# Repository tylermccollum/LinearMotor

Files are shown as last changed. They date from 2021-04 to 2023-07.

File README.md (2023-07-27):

# Axial Linear Motor
A 3D printed linear motor prototype
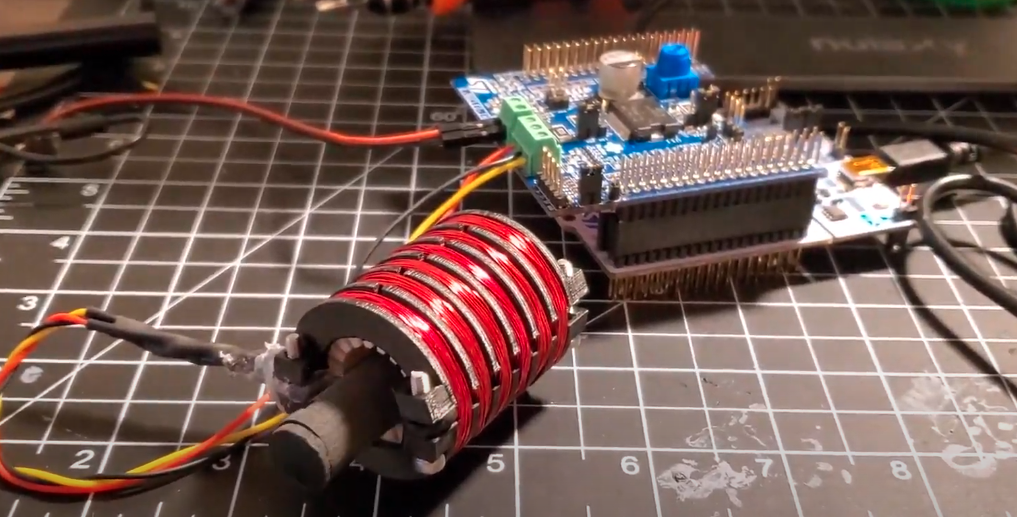
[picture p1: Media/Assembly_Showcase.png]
Assembly


# Background
While the end-goal of many actuators is linear motion, achieving linear motion usually involves a rotary motor and a ball-screw or a spool and cable assembly. While both of those options will suffice for most applications, they significantly increase the complexity of most assemblies and are susceptible to wear. "True" linear motors do exist, but most designs have the coil-magnet flux normal to the path of travel, essentially forming a rotary BLDC motor with an infinite radius. This configuration reduces the efficiency and the force output for a motor of a given size. 

While it is even possible to purchase linear motors where the flux angle is always perfectly aligned (what I'll call "Axial Flux Linear Motors") they're often prohibitively expensive outside of commercial applications and lack potential for customization. The goal for this project is to design a functional, scalable prototype of an axial linear motor that can be re-used in future designs.

# Design
The current iteration of this design is as follows:
- A metal (brass) tube (16mm OD) that will serve as the rail (or piston) for the actuator
- A 3D printed tube to fit inside the rail that will conwtain the magnets
- A polymer linear bearing (Igus 16mm ID) for ease of movement between the carriage and rail
- A carriage formed of two shells that clamp around the bearing
- Three phases of magnet wire that wind around the carriage assembly

Renderings and images of the parts can be seen below:

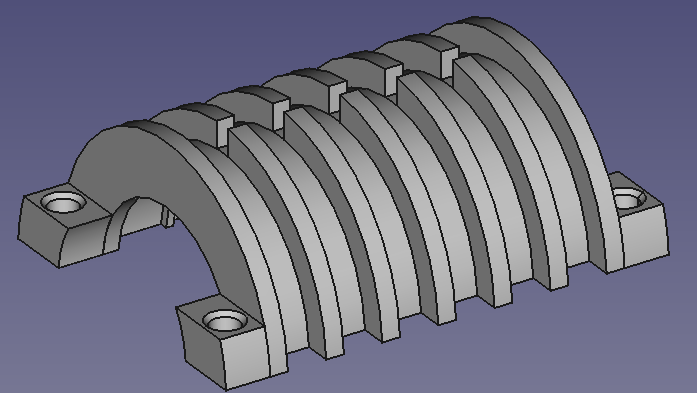
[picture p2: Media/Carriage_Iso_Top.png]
Carriage half rendering


Carriage half body

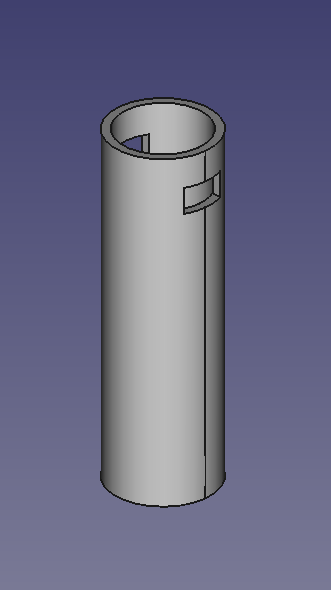
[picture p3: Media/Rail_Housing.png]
Magnet housing rendering


Magnet housing tube body

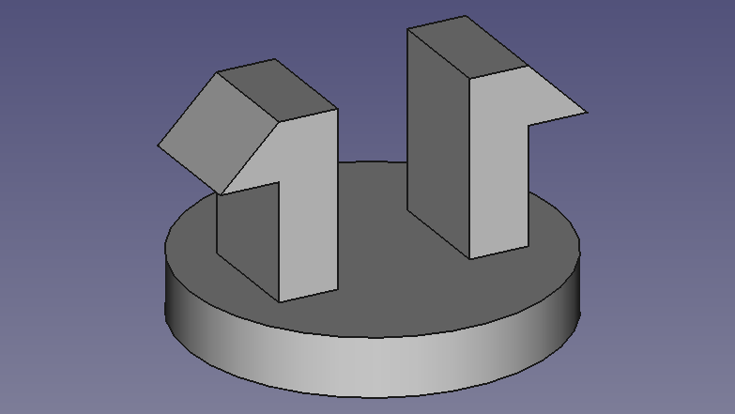
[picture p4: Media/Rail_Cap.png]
Magnet cap rendering


Magnet housing cap

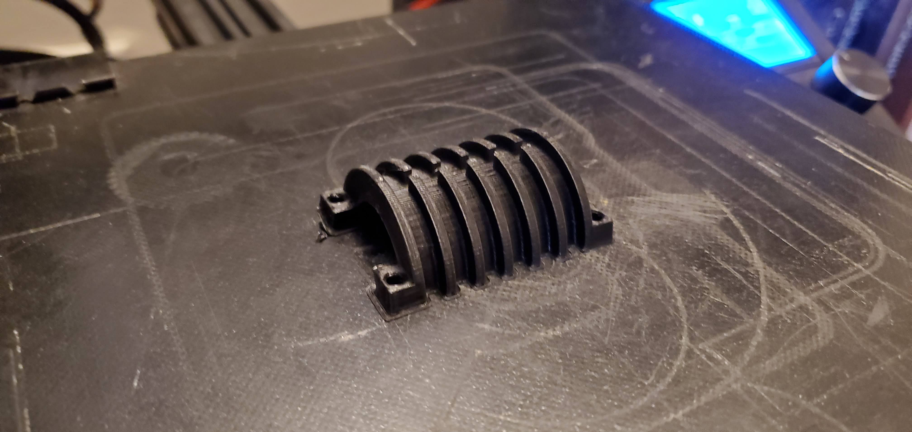
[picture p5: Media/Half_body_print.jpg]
Carriage half

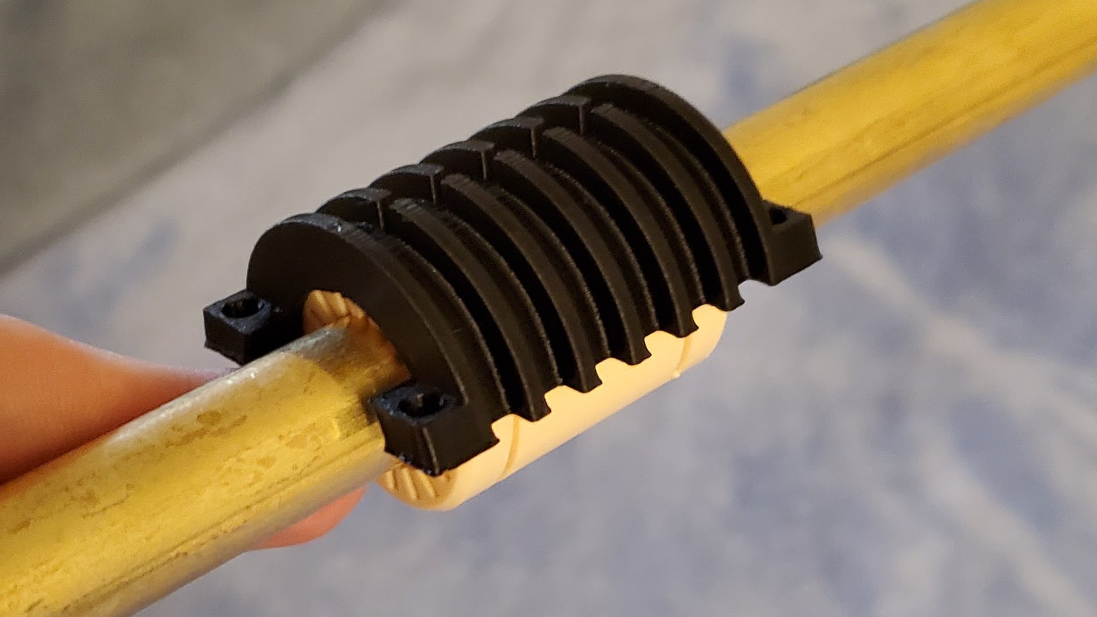
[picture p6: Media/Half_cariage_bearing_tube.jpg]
Carriage half on bearing on rail

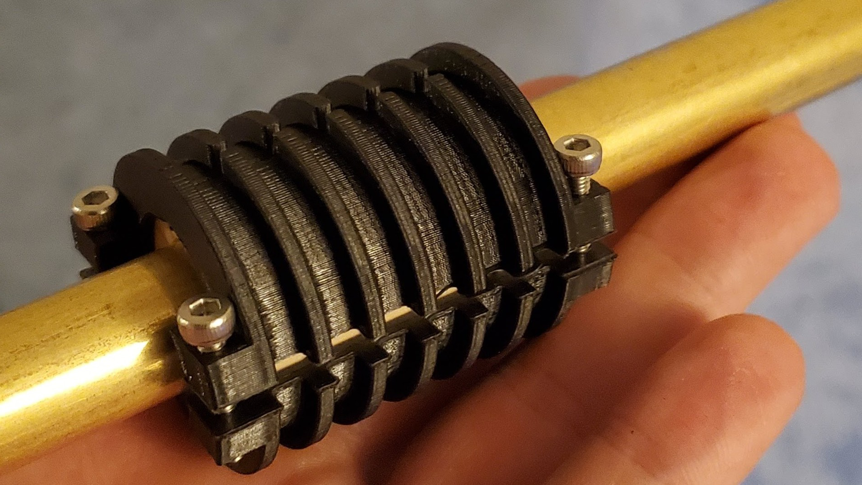
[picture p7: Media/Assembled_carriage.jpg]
Carriage assembly

Carriage with coils
Carriage with coils on rail

# Assembly
The assembly of the 3D printed carriage body is relatively straight-forward: snap the two halves around the bearing and insert 4x M3 screws to hold it together. 

## Carriage
The more difficult portion lies in the winding of the coils. While this would definitely benefit from a video, my best at describing the process is here:

1. For the first phase (A), feed the wire between the halves of the outer body and wrap one end of magnet wire around one of the clamping screws 
2. Wind the coil for as many turns as intended, choosing either clockwise or counter-clockwise *NOTE: All coils must be wound in the same direction*
3. Run the wire through the cut at the top or bottom, skipping 2 rows before bending into the channel- make sure it's in a stable position
4. Feed end of the second phase (B) between the two halves of the outer body and under the first phase, wrap around the same screw to secure
5. Begin winding the coil, ensuring that the wire from the first phase is clamped firmly under this new coil
6. When done winding, repeat step 2
7. Follow step 3, feeding the wire for phase C under both existing phases
8. Wind the coil, then run to the final open channel
9. Pull on phase A to tighten it in the first coil, then wrap the second
10. When done winding, unroll an addional length of wire approximately the length of the carriage and cut the wire from the spool
11. Run this end between the halves of the outer body and under all the coils
12. When through, pull tight to secure the second coil of phase A, then wrap carefully around the clamping screw on this end. Label this wire.
13. Repeat steps 9-12 for phases B and 
14. Tin the ends of the wires and test for phase to phase shorts
15. Twist together and solder the starting ends of the 3 phases
16. Tin, solder, and heatshrink the opposite ends for the 3 phases (I recommend color coding and, as kludgy as it feels, hot glue makes a great strain relief to avoid phase to phase shorts.
 
In the version that can be seen in the video, each coil contains 75 turns of 28AWG wire.
 
## Rail
This part, while conceptually much simpler, is a massive pain. In order to get magnetic "teeth" that the coils can hold on to, the magnets must be put together in an opposition to eachother (i.e. SN-NS-SN-NS...). This can be illustrated with some magnetic viewing film:

Aligned magnets
When aligned naturally, the poles of the magnets "short-out" and essentially form one large magnet

Opposed magnets
But when they're put together in opposition, they become seperable, allowing for the coils to hold the rail/piston in place.

To make the rail, fill the Magnet Housing with as many magnets in opposition as possible, then close the cap (you'll likely want to add glue to ensure it doesn't open, but avoid forming lumps that will catch on the carriage bearing).

The small piston seen in the video only has 4 magnets in it.

# Controls
This one certainly has room for improvement. I'm currently driving it with an X-NUCLEO-IHM07M1 kit and a basic 6-Step commutation. The current iteration of the design does not generate sufficient back-emf on movement, so some sort of encoder will be necessary (or a change to the coil setup, which is more likely)

# Conclusion
The current iteration with coils made from 75 turns of 28AWG wire and a 4 magnet piston can oscillate at up to ~3Hz when run at ~18V, ~1.2A. Exciting for a second iteration (first iteration was 9 turns of 2 24AWG strands: needed way too much current), but definitely a lot of room for improvement.

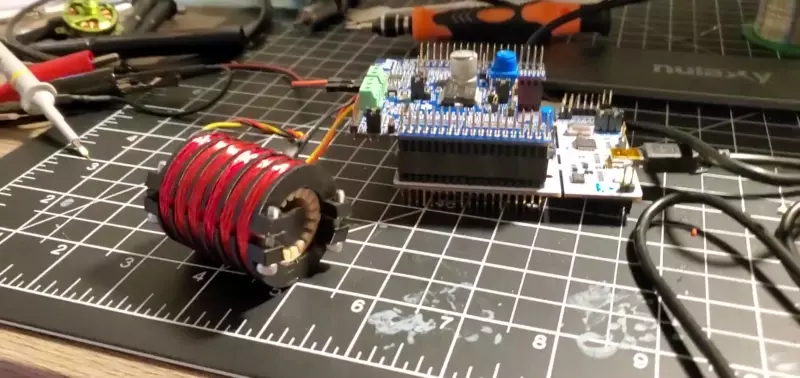
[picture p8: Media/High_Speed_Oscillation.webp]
Motor Oscillating


# Room for improvement
Theres a lot here that will need exploration:
- A greater quantity of shorter phases
- Parametric carriage generation
- More turns of thinner wire
- Stabilized magnets within the rail

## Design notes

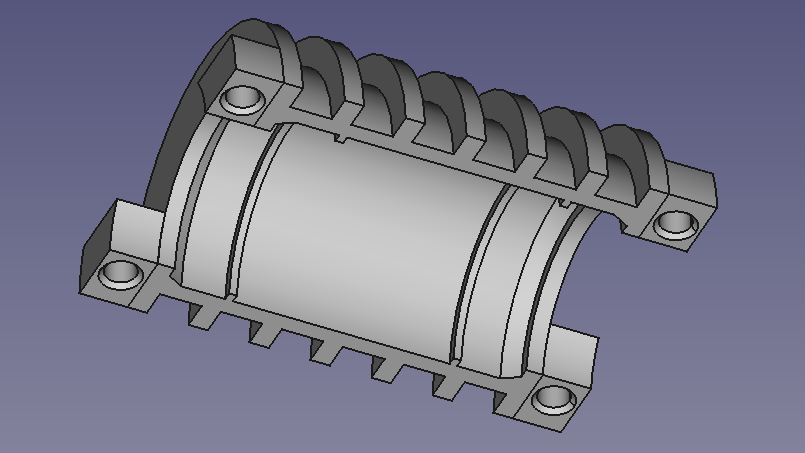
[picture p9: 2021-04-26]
Media/Carriage_Iso_Bottom.png

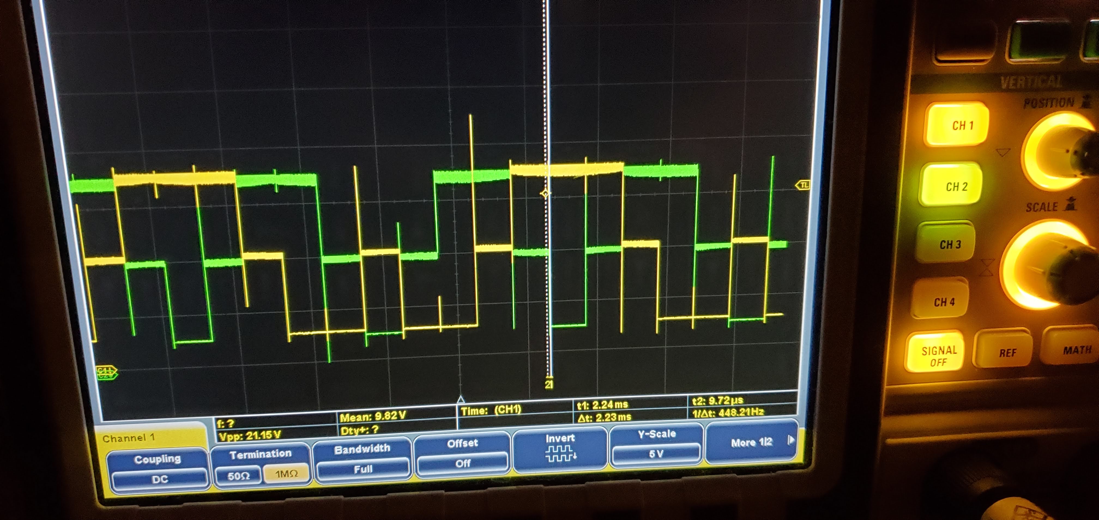
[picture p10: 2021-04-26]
Media/Phase_Voltages.jpg

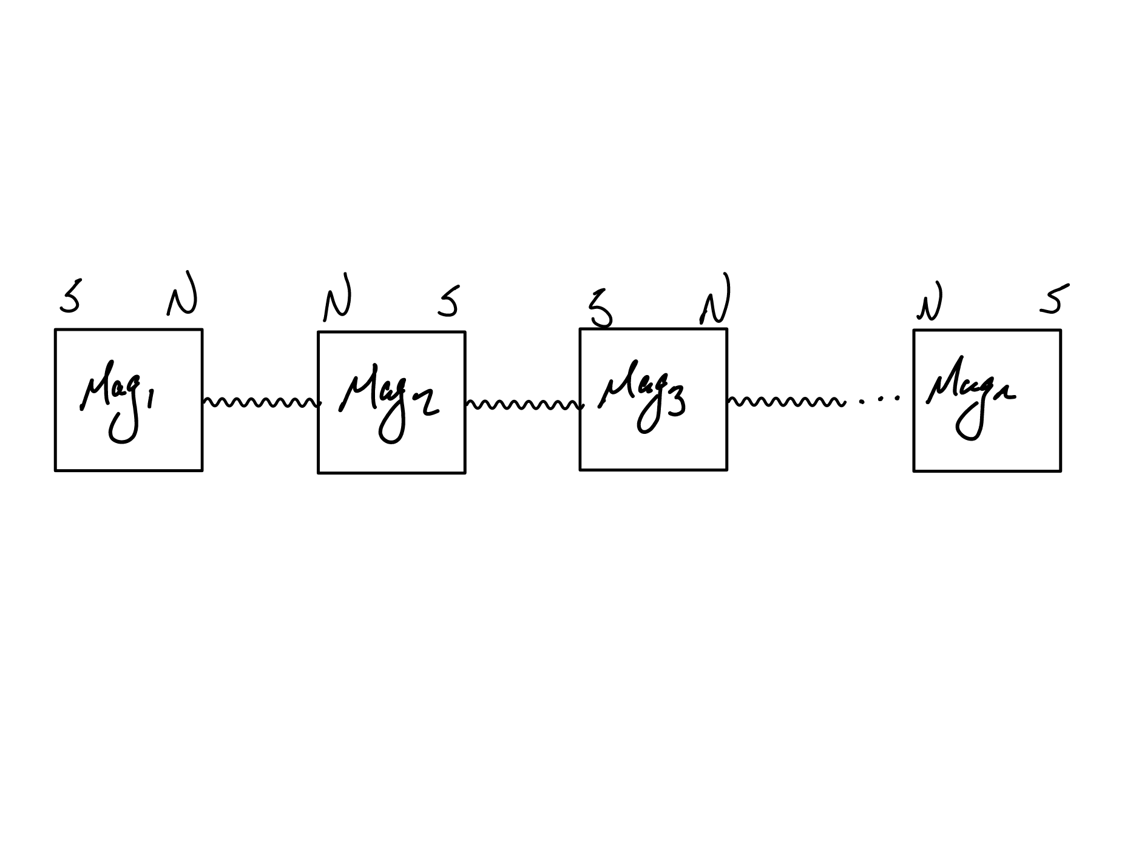
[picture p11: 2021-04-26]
Media/Free_Magnet_Rail.png

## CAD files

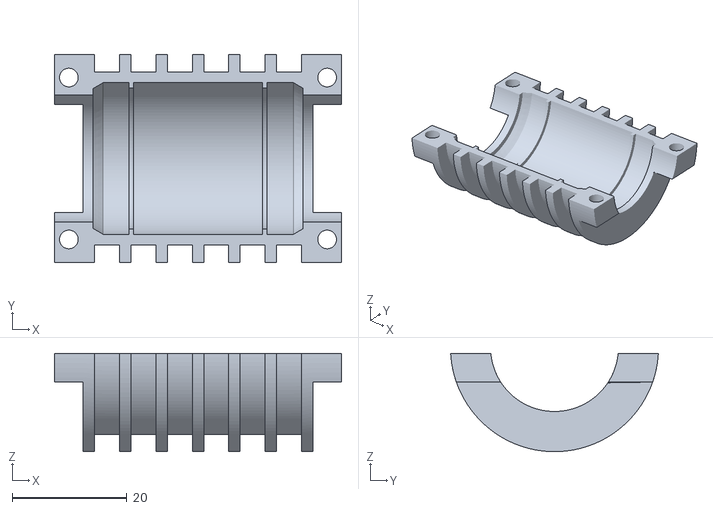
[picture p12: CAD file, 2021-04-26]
CAD/Single Bearing-Body.stl
50.0 x 36.2 x 17.1

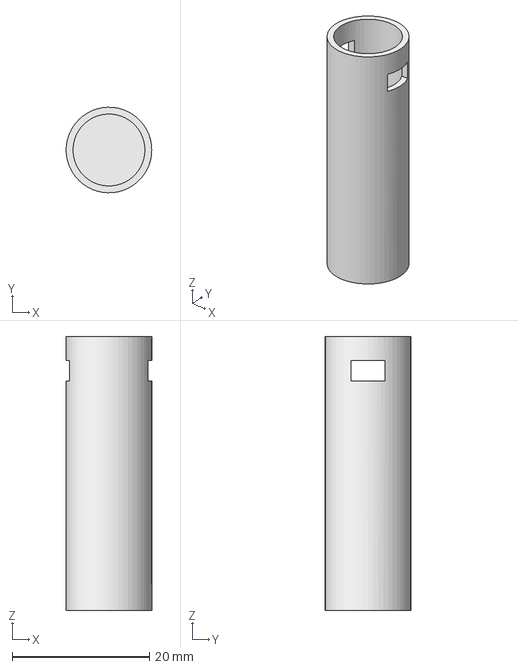
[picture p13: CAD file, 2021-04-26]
CAD/Magnet_Housing.FCStd
12.5 x 12.5 x 40.0 mm

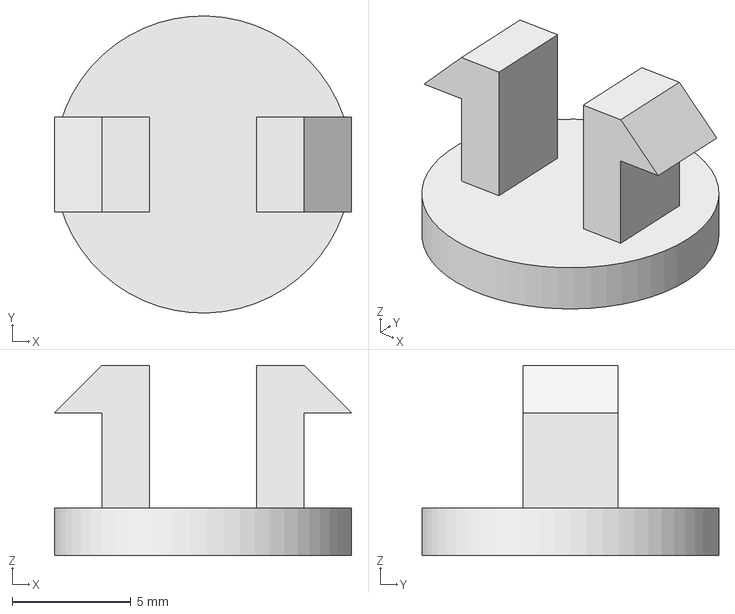
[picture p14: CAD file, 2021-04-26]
CAD/Magnet_Cap.FCStd
12.5 x 12.5 x 8.00 mm

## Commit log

2021-04-26 Add CAD images, illustration of rail
2021-04-26 Upload CAD files
    [Magnet_Cap.FCStd, Magnet_Housing.FCStd, Single Bearing-Body.stl]
